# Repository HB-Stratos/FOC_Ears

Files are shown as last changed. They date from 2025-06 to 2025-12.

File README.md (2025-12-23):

Hi there! Since the below was written, a few more things have happened:

You can **send me your Email if you want to get involved with development** and I'll reach out. [Click Here](https://app.formbricks.com/s/cmjj02hcw36xmad01dme5074u).

Work has also started on a PCB based version. PCBs have been ordered, and may or may not have arrived in time for Congress. \
In any case, you can find all KiCad files [on the rev2 branch](https://github.com/HB-Stratos/FOC_Ears/tree/rev-2).

# FOC Ears: Dead Silent Animatronics, a Prototype

This repository documents my work to create truly silent animatronic cat ears.

The classic design using RC airplane servos is quite noisy, and I wanted to fix that to build animatronics that you can comfortably hold a conversation around.

## Table of Contents

- [FOC Ears: Dead Silent Animatronics, a Prototype](#foc-ears-dead-silent-animatronics-a-prototype)
  - [Table of Contents](#table-of-contents)
  - [Status](#status)
    - [Future Plans](#future-plans)
  - [Documentation](#documentation)
    - [System Overview](#system-overview)
      - [Components](#components)
      - [Motor Assembly](#motor-assembly)
    - [Wiring](#wiring)
    - [3D Prints and Mounting](#3d-prints-and-mounting)
    - [Build Environment Setup](#build-environment-setup)
    - [Misc. Lessons Learned](#misc-lessons-learned)
  - [Thanks](#thanks)
  - [Finally](#finally)

## Status

I managed to create a working prototype in time for GPN23. It has a rather bulky perfboard electronics package and several electronic design limitations, such as the lack of a fuse, but it held up well for the entire event. Unfortunately, my phone died between building the prototype and writing this documentation, so I have lost some work-in-progress photographs. Words and renders will have to suffice.

final product

webp animated video

<details>
<summary>More Pictures (expand)</summary>

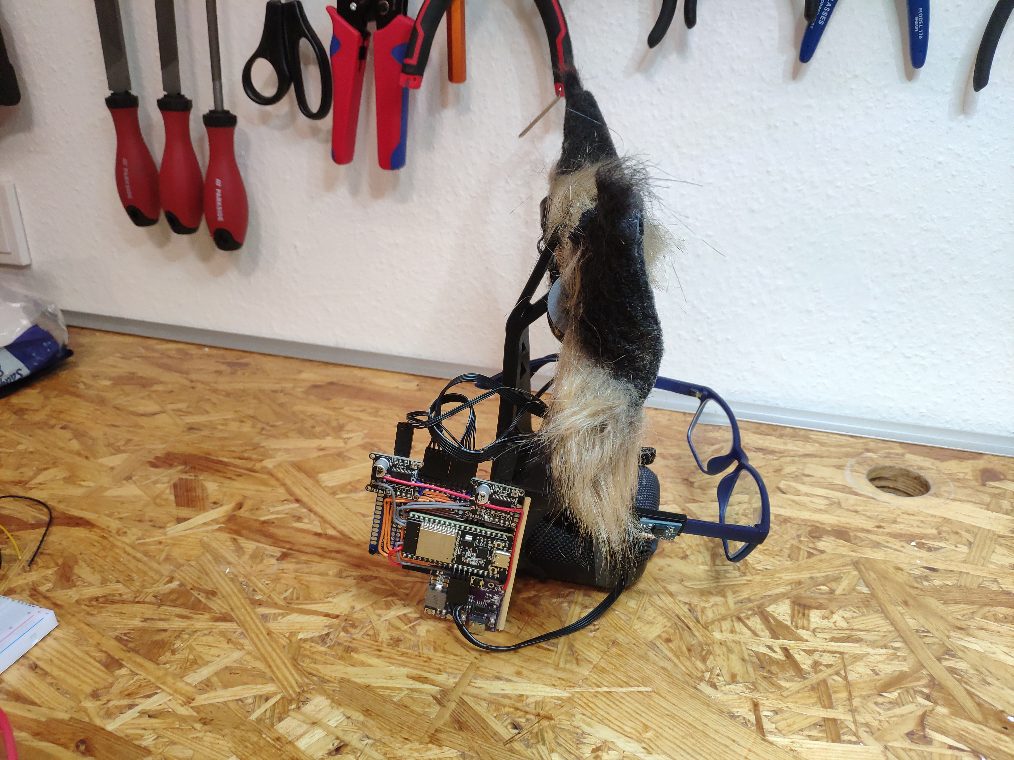
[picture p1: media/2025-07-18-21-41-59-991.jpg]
side view

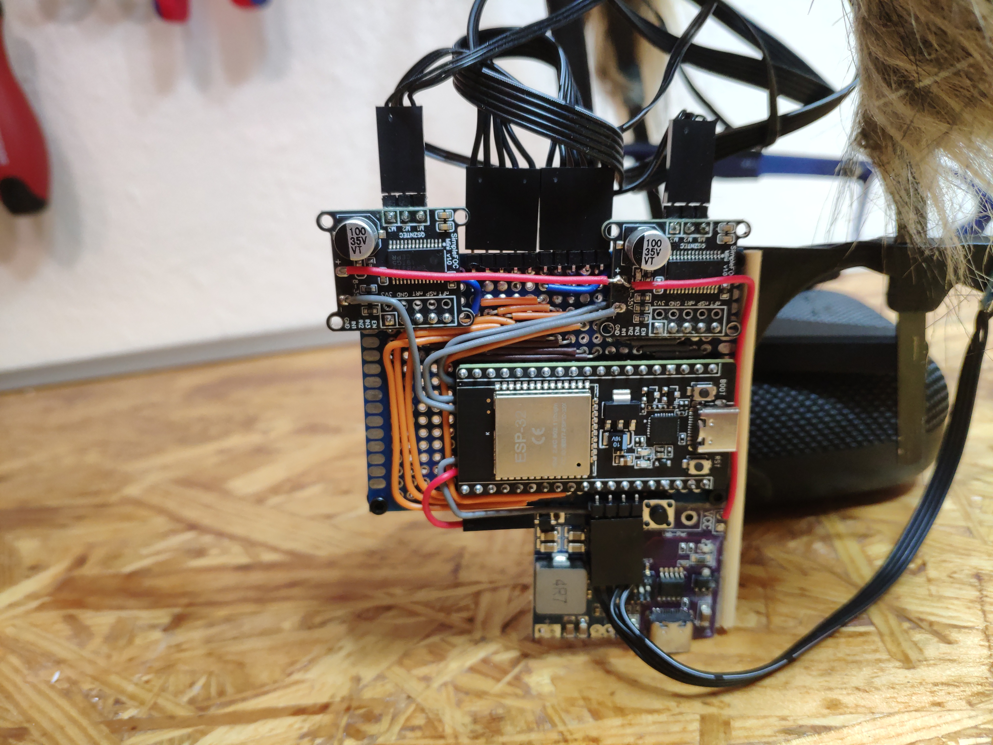
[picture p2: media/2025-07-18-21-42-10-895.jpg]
closeup


</details>

### Future Plans

I plan to develop a more robust version with a printed circuit board between the ears to house the electronics in a much neater way. I would like to eventually create a product out of this development, but even if I do, I plan to keep all design files and details open source.

## Documentation

> [!IMPORTANT] > **This is a prototype**. I am documenting this for sake of posterity. If you wish to replicate this design, you are welcome to do so. However, expect to face issues, poor design decisions and have expect to solve many stupid problems on your own. Because of this, this is not written as a tutorial, but more as an overview of what it takes. That said, I'm happy to help where I can, just leave an issue on the repo here.

With that said, lets get into it

### System Overview

#### Components

The system consists of the following components:

- An [ESP32WROOM](https://aliexpress.com/item/1005008002597306.html) micro controller <br>
  

- Two [SimpleFOC mini](https://docs.simplefoc.com/simplefocmini) driver boards <br>
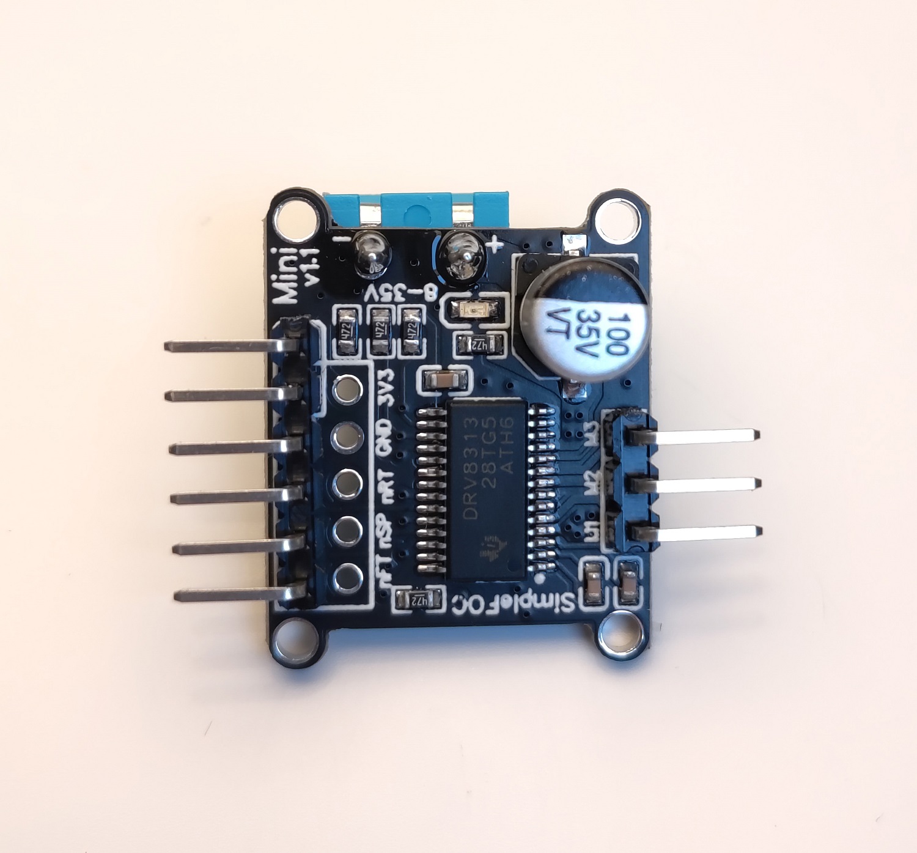
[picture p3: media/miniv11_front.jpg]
  

- Two [Mitoot 2208 100kv](https://aliexpress.com/item/1005006008489660.html) Brushless Gimbal Motors <br>
  

- Two [MT6701qt](https://aliexpress.com/item/1005007349429583.html) Magnetic Encoders <br>
  

- A [BNO055](https://aliexpress.com/item/1005006770124726.html) IMU <br>
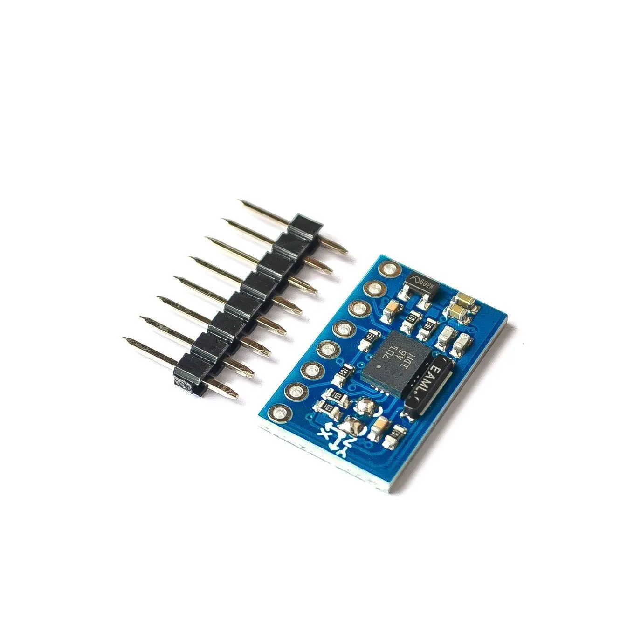
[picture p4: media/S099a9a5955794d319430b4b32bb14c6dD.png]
  

- Ears from Aliexpress. There appears to be a whole range of different style ears on Aliexpress, all following the same basic design. Look for the ears in the ~10€ price class, those will likely be extremely similar to [the ones I used](https://aliexpress.com/item/1005004647818937.html). <br>
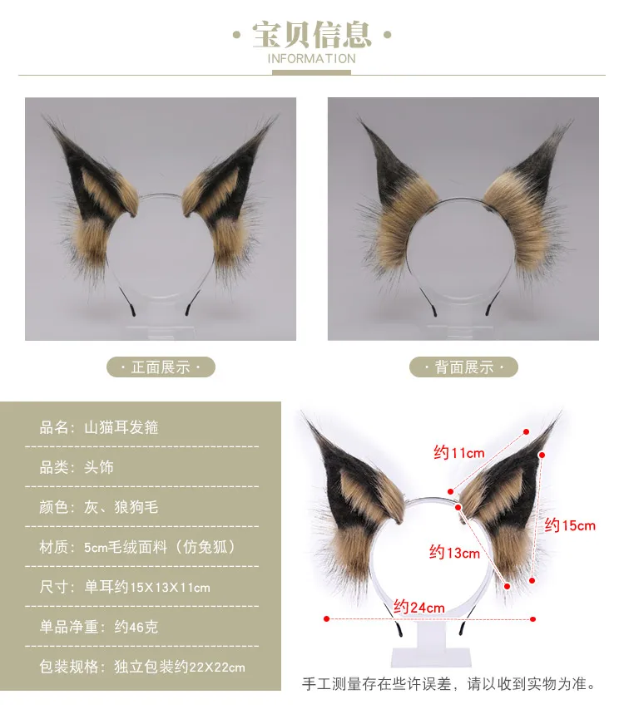
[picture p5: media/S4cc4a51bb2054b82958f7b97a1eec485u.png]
  

- A generic 3.3V Regulator (must be 15V capable)
- A generic configurable USB-C PD trigger board (prototype used 15V)
- A generic USB-C PD capable Power Bank (in my case 100W 20V capable)

Total cost exluding the power bank comes out to ~53€.

Images were taken from their respective linked pages.

> [!NOTE]
> The hardware choices I made worked, but were not ideal:
>
> - The ESP32 can not be flashed without having to hold down the boot button every time
> - The Motors come with the wire through their hub, so one needs to depin the connector, pull the cable through and add the pins again.
> - The Motors are also a bit large, smaller probably works but untested.
> - The Encoder board is undocumented, had to be reverse engineered with the chip data sheet
> - The BNO055 has some hardware issues and is also discontinued, but it was the board I had laying around.

#### Motor Assembly

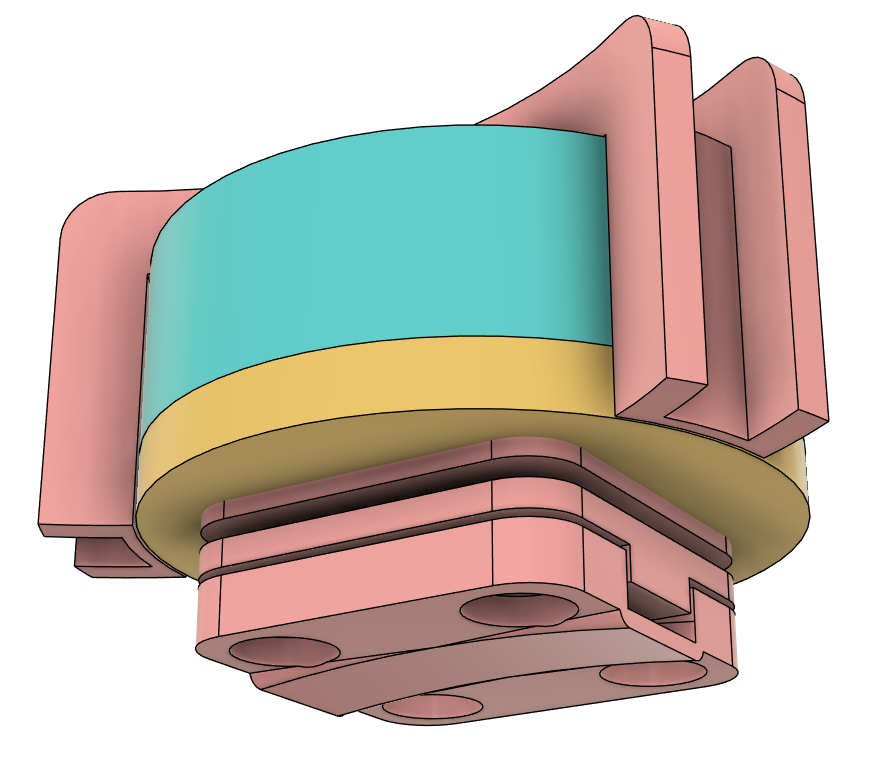
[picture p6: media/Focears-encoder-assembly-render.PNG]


The motor and encoder are mounted together by a stack of parts that clamps the two to each other and the assembly to the head band using all the same screws. The magnet for the encoder is held within the hollow motor shaft by a press fit 3d printed adapter. The ears are mounted on top with two M2x6 screws through the U channel piece.

Ordinarily this wouldn't work as the holes in the motor do not match the holes in the encoder PCB. However there is nothing vital in the ares of the encoder PCB where the holes are needed, so I devised a 3d printed drilling jig to create the required holes. Of course this technique is only applicable to the exact sensor board I used.

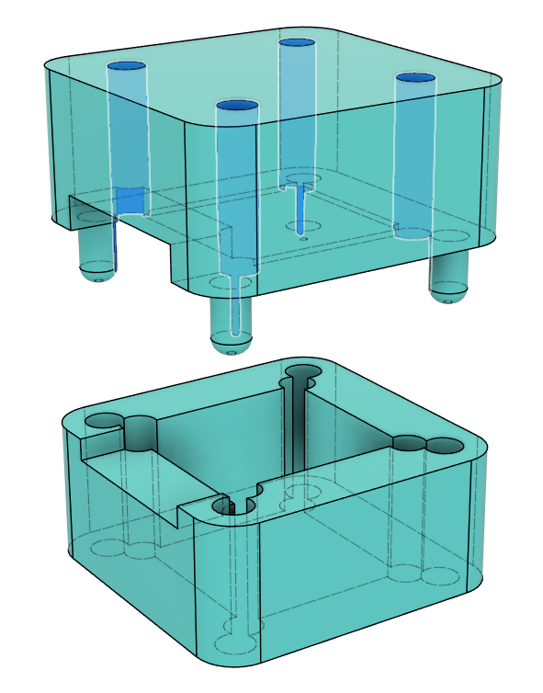
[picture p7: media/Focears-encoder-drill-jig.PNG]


> [!CAUTION]
> Using too long screws to clamp the motor-encoder assembly together will destroy the motor. The holes do not have a backstop, so you will penetrate the coils with the screw. You will not feel rotational resistance as this happens as you are only hitting the stator. I used M2.5x8 screws.

The ears are mounted by making a cutout in them with flush cutters to fit the U channel piece, which is then glued into place with super glue. It is vital that this cut is deeper than the u channel such that the outer edges of the ear sit as flush as possible to the head band. The U channel does not extend all the way down as it would snag on the motor cables if it did.

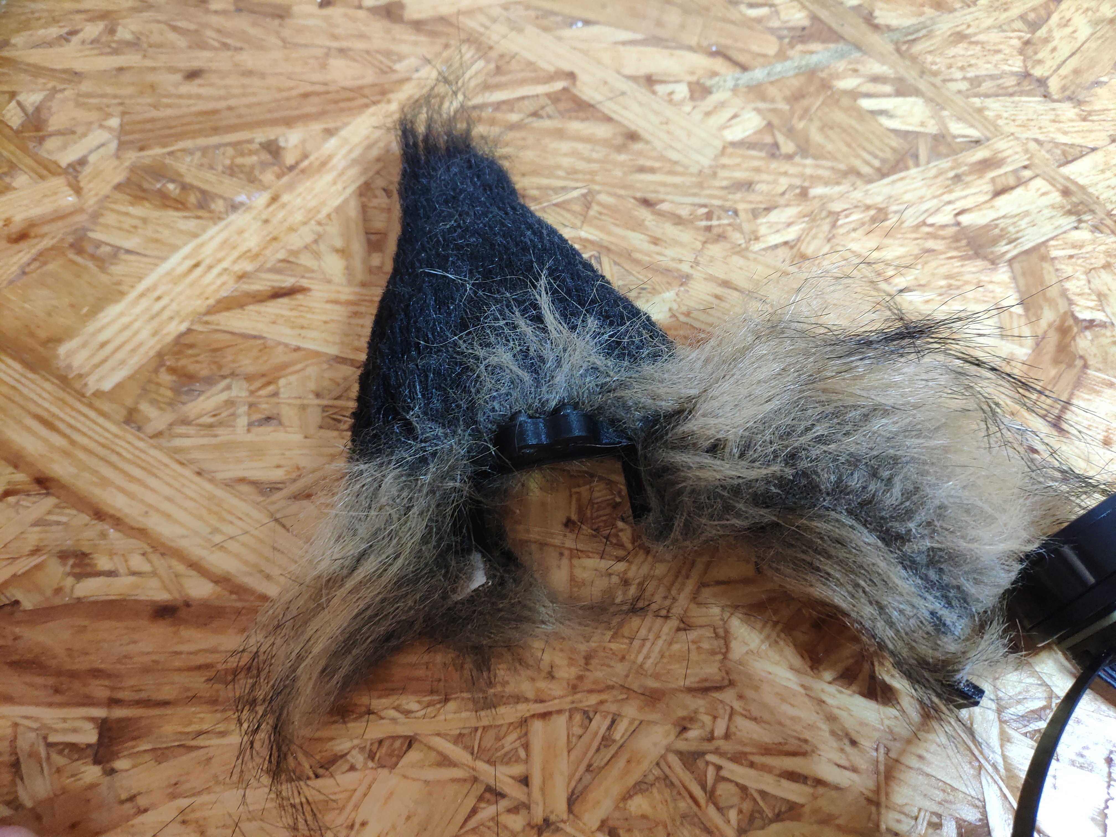
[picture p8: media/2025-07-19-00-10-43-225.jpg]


Additionally, for secondary motion the lower ear lobe of each ear is mounted to a slider on the head band. This causes the ear to fold on rotation, which looks much more natural than the long ear lobe swinging backwards. This however has the issue that the aliexpress ears come with thick wire in them for posing, which would prevent this motion. The solution is as simple as it is ugly: fatigue cracking the wire every 5 or so mm with pliers within the area that should bend. The slider is printed from TPU for silent motion and (surprisingly) low friction.

> [!NOTE]
> I have tried to completely remove the wire from the ears. The wire is hot glued in place within the ears in multiple places, and the fur is bonded together firmly. Even by cutting along the edge of the ear all the way around I was not able to extract the wire in the base of the ear, and said cut looked quite ugly and would have been hard to close up again. Hence I deemed it better to leave the wire in place, but fatigue crack it where necessary. A less hand-fatiguing solution is definitely needed for higher volume production though.

The ear detached from the motor, with lines highlighting roughly where I broke the internal wire. Also visible is the TPU slider, here detached from the rail.



### Wiring

PowerPoint graphic design is my passion. Not pictured are 3.3v running to all sensors, shared ground between all and a 2.2k pullup resistor between SDA and 3.3V on the BNO055. Additionally, note that I used SimpleFOC Mini 1.0 driver boards as they were easily available on Aliexpress. SimpleFOC Mini 1.1 drivers are similar, but their pin order appears to be flipped.

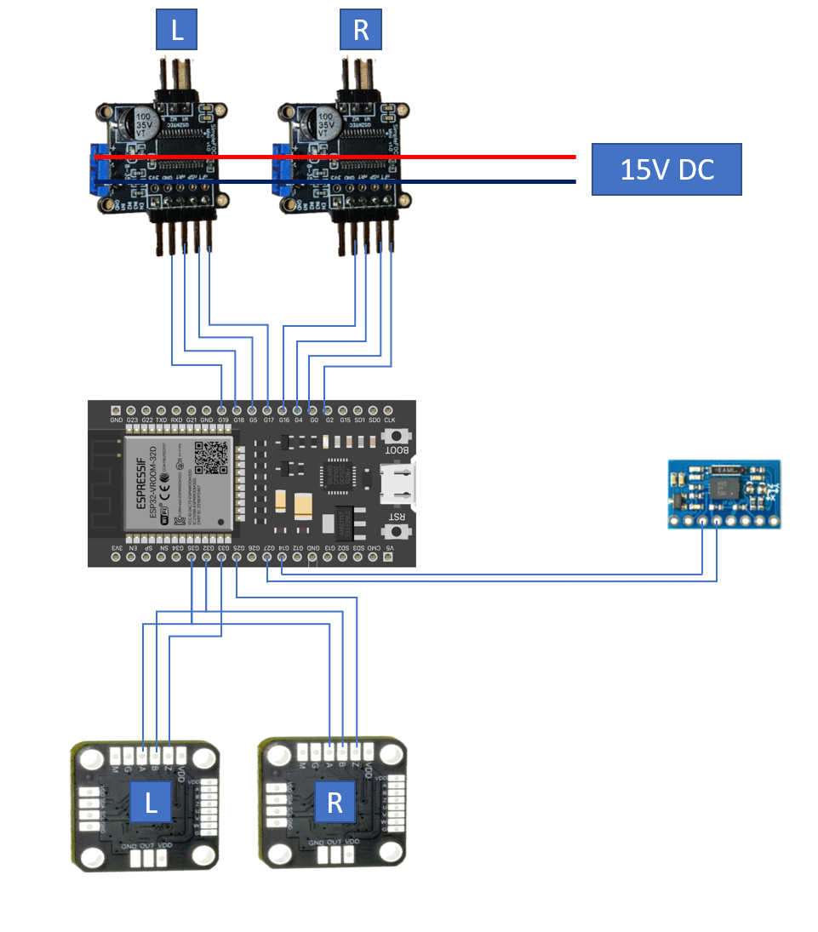
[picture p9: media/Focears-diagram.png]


Here's the reverse-engineered diagram for the encoder. Also, [here's the datasheet](https://uploadcdn.oneyac.com/attachments/files/brand_pdf/magntek/F3/CA/MT6701QT-STD.pdf).

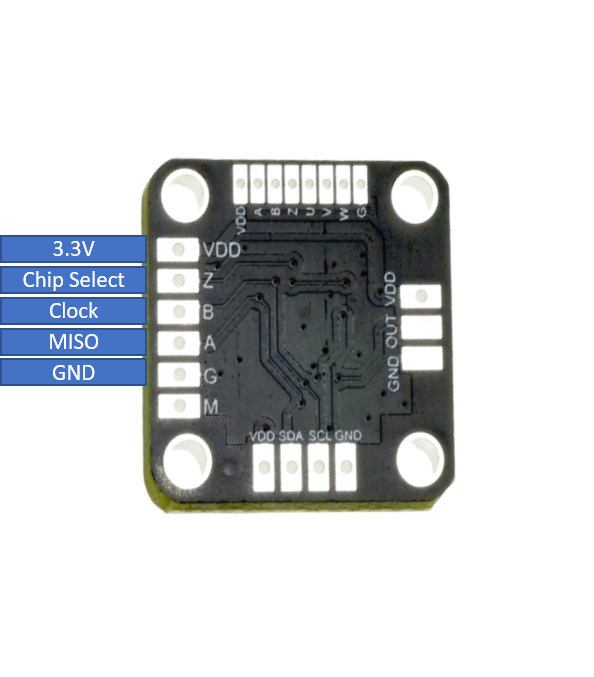
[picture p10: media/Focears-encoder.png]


> [!NOTE]
> This encoder is supposedly capable of I2C and SSI (we use SSI), and CS would toggle between the two modes. However this would cause bad I2C writes on the shared SSI bus with CS off, which I have heard reported, but could never observe myself. I can only assume my specific board has some resistors onboard that disable I2C.

A closeup of the final breadboard. Unsurprisingly, gluing circuit boards together edge to edge did not prove to be particularly sturdy, and the design made the USB-C cable start uncomftably low. But it did work.



### 3D Prints and Mounting

This is the mount for the board, based of my earlier design of ear hook glasses clips to mount non-animatronic ears. This glasses clip is desiged for my glasses (Zenni Optical [Navy Rectangle Glasses #2018916](https://www.zennioptical.com/p/tr-rectangle-eyeglass-frames/20189/2018916) ), so if these do not also happen to be your glasses you will have to devise a custom mounting solution. I am yet to come up with a generic solution that would work with all glasses while still looking good.

Also, this piece is a royal pain to print as one might expect. The first print of it I did completed, but all five attempts to print a spare piece before the event failed.

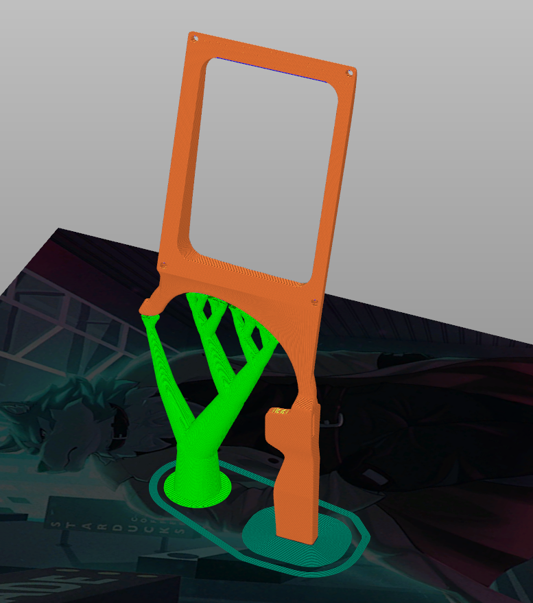
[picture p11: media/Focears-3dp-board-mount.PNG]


The parts constituting one motor-encoder-ear sandwich, laid out in the orientation I printed them in.

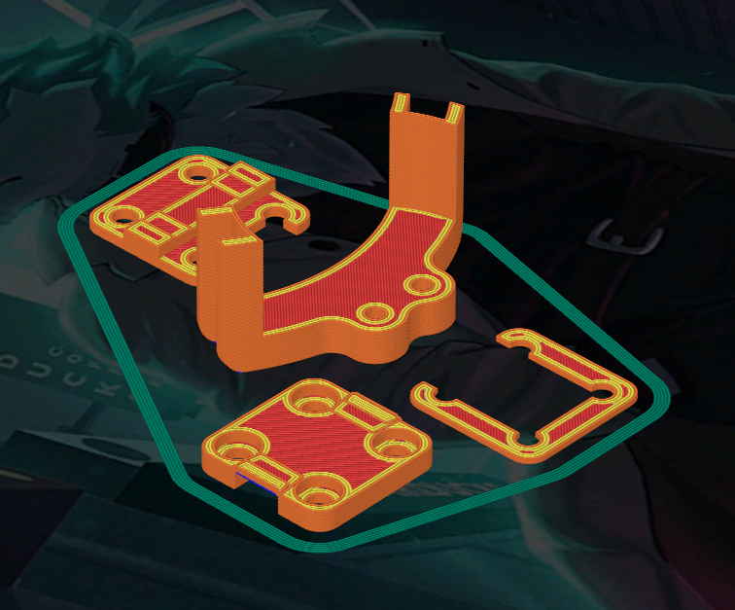
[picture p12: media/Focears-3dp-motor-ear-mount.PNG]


The ear lobe slider which glides on the metal headband. It is printed from TPU for silent motion. Earlier prototypes showed that even the slightest bit of noise so close to the wearer's ear is quite annoying.

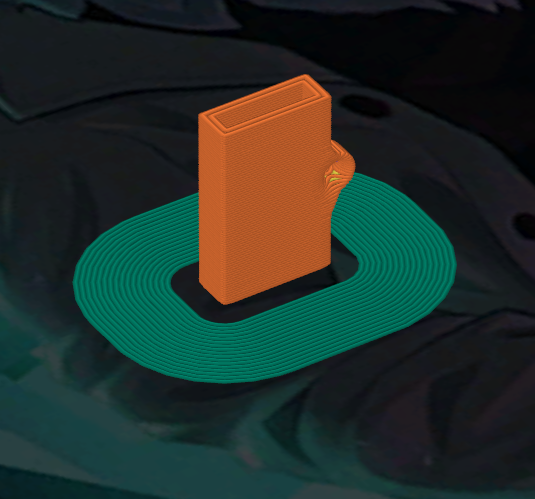
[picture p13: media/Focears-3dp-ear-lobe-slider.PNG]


All 3d printed parts can be found in the `printed_parts` directory as STEP files, as well as the original Fusion360 source files. Do note however that the source files are a royal mess as they were created during prototyping and with exactly zero patience.

### Build Environment Setup

This project uses PlatformIO instead of the Arduino IDE as it has far superior code completion and extension support. Setting up the build environment should just be as easy as setting up PlatformIO using the [official guide](https://docs.platformio.org/en/latest/integration/ide/vscode.html#quick-start) and cloning this repository into the workspace. It will take a few minutes to load, but PlatformIO should automatically download all required frameworks and libraries as specified in the `platformio.ini` file. If this doesn't work for whatever reason, please do open an issue. Also, for some reason this was removed from the official settings, but PlatformIO does offer an "Upload and Monitor (connect to Serial Monitor immediately)" mode. You can find out how to set this up [here](https://community.platformio.org/t/shortcut-to-upload-and-monitor-task-while-also-restarting-it-if-active/18104/5).

### Misc. Lessons Learned

- If the screws clamping the encoder to the motor are not tight enough, the motor likes to shake itself to bits as it twisting against the encoder causes a feedback loop.
- If the screws clamping the encoder to the motor are too tight, they can stretch a poorly printed plastic clamp and make the mounting screws penetrate the motor core.
- Having a cheap oscilloscope ([Zoyi ZT-703S](https://aliexpress.com/item/1005006593085723.html), ~80€) was invaluable during development, you likely want one too.
- At least on my BNO055 board the I2C pullups were too weak for high frequencies, an external pullup was needed.
- Having a Dupont connector crimping tool is quite useful.
- Surprisingly, the mess of wires going from the sensors and motors to the perfboard never got tangled. Still, they're a bad design.
- Having any D term in the PID motion controllers makes the motor quite noisy.
- High loop speed of the main FOC loop is important for precise and silent control.
- Any change in loop speed also constitutes a change in optimal PID values, a fixed loop speed would be a good code design choice I did not make.
- A RP2040 has pretty low loop speed due to lack of a hardware floating point unit, not ideal for this application.
- Many in and output pins are needed to control the motors, 4 per motor driver, one per sensor plus two more sensor shared pins, plus the I2C pins for the IMU. I almost ran out of useable IO pins on the ESP32.
- Reading the IMU every loop slows the motor control loop down too much, reading the IMU every 10 ms was found to be sufficient.
- A PT1 filter element was integrated into the motor driver to limit maximum acceleration, safeguarding from a position step input being too violent.
- The clamping pieces should be printed from ASA or similar, especially during testing or with a sensor error, the motors can get quite hot.
- The metal hoop that comes with the aliexpress cat ears is bent outwards at the bottom. Bending it straight makes sliding mounts with much tighter tolerances on possible.
- Fatigue cracking the ears works, but likes to compress the fur under the pliers. Scratching it with finger nails appears to restore most of the fluff.
- Mounting the ears to my glasses proved essential. The motors are not the lightest, and with my mounting solution clipping onto my glasses and hooking behind my ears, I never feared losing the ears. I am yet to come up with a solution that would work for all glasses frames, let alone a solution for people who do not wear glasses.
- Espressif changed something in more recent versions of the framework, which broke SimpleFOC. It either doesn't compile or kernel panics. I went and found the newest version released before the latest SFOC release, which worked well. You can find the details in the platformio.ini file.
- SimpleFOC requires that PlatformIO `lib_archive = false`. If it isn't your code will compile and run, but behave weirdly in all sorts of strange ways. Be careful.
- The Motors claim they can handle 12V, but I have driven them to 20V with no issues. I just went with 15V as I didn't need the torque and it slowed the motor heating up should an ear become blocked.
- This project started with me trying to use silent stepper drivers and motors for the motion instead of FOC. However, the holding current being constantly drawn by the stepper motors made them get very hot while still lacking torque to not miss steps. Still, using TMC2209 stepper drivers might work for smaller animatronics such as blinking eyes.
- If you can't upload the code with error Access Denied, check if you have a 3D printer slicer such as Cura open. It was automatically trying to connect to all COM ports for me, blocking code uploads.

## Thanks

to everyone who helped me with this project. Especially the amazing people of the Voidstarlab and SimpleFOC discord who took their time to not only help me debug problems with my motor setup, but also with reverse engineering the Encoder PCB, debugging the IMU and many other hardware engineering issues unrelated to SFOC. This was my first true hardware engineering project. I learned a ton, and I couldn't have done it without y'all.

## Finally

Overengineer more silly projects, build cool stuff, and have fun!

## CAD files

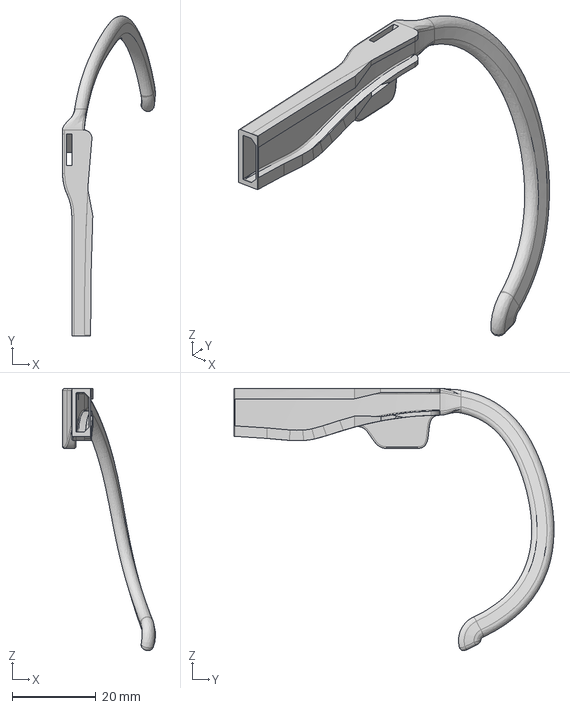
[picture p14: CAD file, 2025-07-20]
printed_parts/FOCEars-glasses-clip-empty.step
22.2 x 76.4 x 62.6 mm

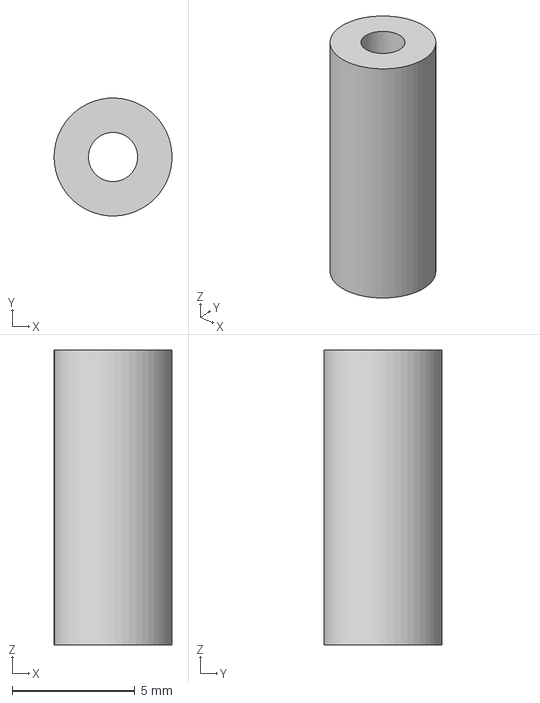
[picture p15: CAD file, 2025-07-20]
printed_parts/FOCEars-motor-encoder-magnet-insert.step
4.80 x 4.80 x 12.0 mm

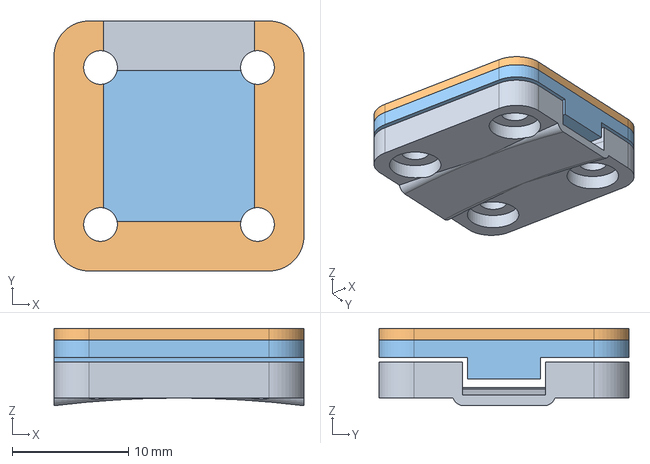
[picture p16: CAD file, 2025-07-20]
printed_parts/FOCEars-motor-mounting-pieces.step
21.5 x 21.5 x 6.66 mm

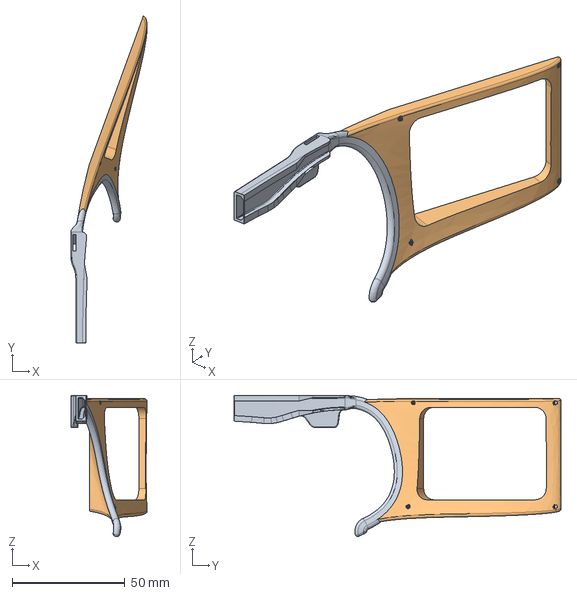
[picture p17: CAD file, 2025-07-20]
printed_parts/FOCEars-glasses-clip-pcb-mount.step
33.9 x 145.0 x 62.6 mm

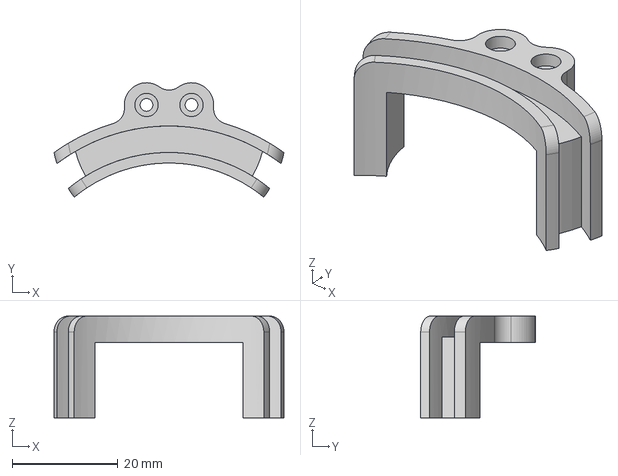
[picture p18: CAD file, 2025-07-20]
printed_parts/FOCEars-u-channel-ear-mount.step
43.5 x 21.6 x 19.2 mm

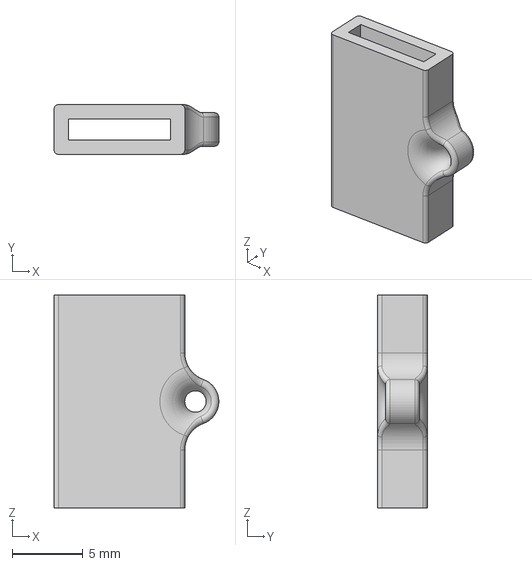
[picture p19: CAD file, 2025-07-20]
printed_parts/FOCEars-tpu-ear-lobe-slider.step
11.6 x 3.50 x 15.0 mm

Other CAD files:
printed_parts/Ear Mount v3.f3z
printed_parts/Ear Silent Slider v3.f3d
printed_parts/Mitoot 2804 Encoder Mount v14 (encoder magnet pin).f3d
printed_parts/Mitoot 2804 Motor Mount v14.f3d
printed_parts/glasses clip v27.f3d

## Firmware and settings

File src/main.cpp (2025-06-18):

#include "Arduino.h"
#include "SPI.h"
#include "SimpleFOCDrivers.h"
#include "encoders/MT6701/MagneticSensorMT6701SSI.h"
#include "EarController.h"
#include <Wire.h>
#include <Adafruit_Sensor.h>
#include <Adafruit_BNO055.h>
#include <IMUHandler.h>
#include <MathHelpers.h>

#define PIN_BUTTON 13

#define I2C_SDA 27
#define I2C_SCL 14

TwoWire I2CBNO = TwoWire(0);
IMUHandler imuHandler(&I2CBNO, 0.5);

EarController earL = EarController(33, 19, 18, 05, 17, 0.1, -1.9);
EarController earR = EarController(25, 16, 04, 00, 02, 0.1, -1.9);

unsigned long leftFlickStartTime = 0;
unsigned long rightFlickStartTime = 0;
const int FLICK_DURATION_MS = 200; // Longer duration for full wave

const unsigned long BUTTON_HOLD_DURATION = 1000; // 1 second in milliseconds
bool buttonPressed = false;
unsigned long buttonPressStartTime = 0;
bool toggleState = false;

float calculateFlick(float progress)
{
    return 0.8f * exp(-4 * progress) * sin(progress * PI * 2);
}

void setup()
{
    Serial.begin(115200);

    I2CBNO.begin(I2C_SDA, I2C_SCL, 100000);
    /* Initialise the sensor */
    if (!imuHandler.init())
    {
        Serial.println("IMU initialization failed!");
        while (1)
            ; // Halt execution if initialization fails
    }

    Serial.println("IMU initialized successfully!");

    /* Initialize Push Button */
    pinMode(PIN_BUTTON, INPUT_PULLUP);

    /* Initialize Ear Controllers */
    earL.setHomePos(0.5);
    earR.setHomePos(-2.9);

    earL.init(2.14, Direction(-1));
    earR.init(1.98, Direction(-1));

    // earL.init();
    // earR.init();
}

unsigned long lastImuUpdate = 0;
unsigned long lastPrintTime = 0;

void loop()
{
    if (digitalRead(PIN_BUTTON) == LOW) // Button is pressed (active LOW)
    {
        if (!buttonPressed)
        {
            // Button just pressed
            buttonPressed = true;
            buttonPressStartTime = millis();
        }
        else
        {
            // Check if button held long enough
            if ((millis() - buttonPressStartTime) >= BUTTON_HOLD_DURATION)
            {
                toggleState = !toggleState; // Flip the toggle
                // Reset timer to prevent multiple toggles
                buttonPressStartTime = millis();
            }
        }
    }
    else
    {
        buttonPressed = false;
    }

    float targetAngle = 0.1 * PI * _sin(float(millis()) / 500 * PI);
    float targetR = 0;
    float targetL = 0;

    // Use toggleState instead of direct button reading
    if (toggleState)
    {
        targetL =
            +utils::remap_clamped(imuHandler.getAbsoluteRotation().z(), -0.8, -PI / 2, 1, 0.1) + utils::remap_clamped(imuHandler.getAbsoluteRotation().y(), PI / 2, -0.1, 0.9, 0);

        targetR =
            +utils::remap_clamped(imuHandler.getAbsoluteRotation().z(), -PI + 0.8, -PI / 2, 1, 0.1) + utils::remap_clamped(imuHandler.getAbsoluteRotation().y(), PI / 2, -0.1, 0.9, 0);

        unsigned long currentTime = millis();

        // Initiate new flicks
        if (random(100000) < 5 && currentTime - leftFlickStartTime > FLICK_DURATION_MS)
        {
            leftFlickStartTime = currentTime;
        }
        if (random(100000) < 5 && currentTime - rightFlickStartTime > FLICK_DURATION_MS)
        {
            rightFlickStartTime = currentTime;
        }

        // Apply flick animations
        if (currentTime - leftFlickStartTime < FLICK_DURATION_MS)
        {
            float progress = float(currentTime - leftFlickStartTime) / FLICK_DURATION_MS;
            targetL += calculateFlick(progress);
        }

        if (currentTime - rightFlickStartTime < FLICK_DURATION_MS)
        {
            float progress = float(currentTime - rightFlickStartTime) / FLICK_DURATION_MS;
            targetR += calculateFlick(progress);
        }
    }

    // earL.moveTo(targetAngle);
    // earR.moveTo(targetAngle);

    earL.move01(targetL);
    earR.move01(1 - targetR);

    earL.update();
    earR.update();

    if (millis() - lastImuUpdate >= 10)
    {
        imuHandler.update();
        lastImuUpdate = millis();
    }

    if (millis() - lastPrintTime >= 100)
    {
        // Serial.print("L: ");
        // Serial.print(earL.getAngle());
        // Serial.print(" R: ");
        // Serial.print(earR.getAngle());
        Serial.print(" Target: ");
        Serial.print(targetAngle);
        // Serial.println("");

        lastPrintTime = millis();

        imu::Vector<3> var = imuHandler.getAbsoluteRotation();
        Serial.print("X: ");
        Serial.print(var.x());
        Serial.print(" Y: ");
        Serial.print(var.y());
        Serial.print(" Z: ");
        Serial.print(var.z());
        Serial.println("");
    }

    /* Absolute Rotations:
    X: Pitch, zero @ 180, pitch up is decrease
    Y: Roll, zero @ -90, roll right is increase
    Z: Yaw, zero irrelevant
    */

    /*Angular Velocities:
    X: Yaw
    Y: Roll, roll right is increase
    Z: Pitch, pitch up is increase
    */

    /*Linear Accelerations:
    X: Up, upwards is positive
    Y: Forwards, forward is negative
    Z: Rightwards, right is negative
    */

    // _delay(100);
}

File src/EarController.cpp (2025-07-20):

#include "EarController.h"

// Constructor
EarController::EarController(int senCs, int pwm1, int pwm2, int pwm3, int drvEnable, float minAngle, float maxAngle)
    : myMT6701SPISettings(4000000, MT6701_BITORDER, SPI_MODE2),
      sensor(senCs, myMT6701SPISettings),
      driver(pwm1, pwm2, pwm3, drvEnable),
      motor(7, 11.2, 80, 0.003),
      lpf(0.02),
      minAngle(minAngle), // Initialize minAngle
      maxAngle(maxAngle)  // Initialize maxAngle
{
    DEBUG_PRINT("EarController initialized.");
}

// Destructor
EarController::~EarController()
{
    DEBUG_PRINT("EarController destroyed.");
}

// Public function: Initialize the controller
void EarController::init(float zero_electric_offset, Direction sensor_direction)
{
    DEBUG_PRINT("Initializing EarController...");

    motor.zero_electric_angle = zero_electric_offset;
    motor.sensor_direction = sensor_direction;

    // MOSI is not used at all, but has to be specified
    SPI.begin(32, 35, 33); // TODO clean up SPI bus
    configureDriver();
    configurePID();

    motor.linkSensor(&sensor);
    motor.linkDriver(&driver);

    sensor.init();
    driver.init();
    motor.init();

    if (motor.initFOC())
        Serial.println("FOC init success!");
    else
    {
        Serial.println("FOC init failed!");
        return;
    }

    DEBUG_PRINT("Sensor electric offset: ");
    DEBUG_PRINT(motor.zero_electric_angle);
    DEBUG_PRINT("Sensor Direction: ");
    DEBUG_PRINT(motor.sensor_direction);

    DEBUG_PRINT("Initialization complete.");
}

// Public function: Move to a specific angle
void EarController::moveTo(float targetAngle)
{
    motor.move(lpf(targetAngle));
}

// Public function: Move between minAngle and maxAngle based on input [0, 1]
void EarController::move01(float input)
{
    float targetAngle = utils::remap_clamped(input, 0.0f, 1.0f, minAngle, maxAngle);
    motor.move(targetAngle);
}

// Public function: Update the motor state
void EarController::update()
{
    motor.loopFOC();
}

void EarController::setHomePos(float homeAngle)
{
    motor.sensor_offset = homeAngle;
}

float EarController::getAngle()
{
    sensor.update();
    return sensor.getAngle();
}

// Setters for minAngle and maxAngle
void EarController::setMinAngle(float angle)
{
    minAngle = angle;
}

void EarController::setMaxAngle(float angle)
{
    maxAngle = angle;
}

// Private function: Configure the driver
void EarController::configureDriver()
{
    DEBUG_PRINT("Configuring driver...");

    // pwm frequency to be used [Hz]
    driver.pwm_frequency = 24000;
    // power supply voltage [V]
    driver.voltage_power_supply = 15;
    // Max DC voltage allowed - default voltage_power_supply
    driver.voltage_limit = 15;
}

// Private function: Configure PID settings
void EarController::configurePID()
{
    DEBUG_PRINT("Configuring PID...");

    // set control loop type to be used
    motor.controller = MotionControlType::angle;

    // velocity PID controller parameters
    // default P=0.5 I = 10 D =0
    motor.PID_velocity.P = 0.02;
    motor.PID_velocity.I = 2;
    motor.PID_velocity.D = 0.00;
    // jerk control using voltage voltage ramp
    // default value is 300 volts per sec  ~ 0.3V per millisecond
    motor.PID_velocity.output_ramp = 0;

    // velocity low pass filtering
    // default 5ms - try different values to see what is the best. m,
    // the lower the less filtered
    motor.LPF_velocity.Tf = 1 / (6.28 * 200);

    // setting the limits
    // either voltage
    // motor.voltage_limit = 10; // Volts - default driver.voltage_limit
    // // of current
    // motor.current_limit = 2; // Amps - default 0.2Amps

    // angle PID controller
    // default P=20
    motor.P_angle.P = 20;
    motor.P_angle.I = 0; // usually only P controller is enough
    motor.P_angle.D = 0; // usually only P controller is enough
    // acceleration control using output ramp
    // this variable is in rad/s^2 and sets the limit of acceleration
    motor.P_angle.output_ramp = 0; // default 1e6 rad/s^2

    // angle low pass filtering
    // default 0 - disabled
    // use only for very noisy position sensors - try to avoid and keep the values very small
    motor.LPF_angle.Tf = 0; // default 0

    // setting the limits
    //  maximal velocity of the position control
    motor.velocity_limit = 10000; // rad/s - default 20

    // motor.PID_velocity.limit = 1;
    // motor.P_angle.limit = 200;
}

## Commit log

2025-06-18 update filter plotter still broken
2025-06-18 made button toggle
2025-07-20 (finally) wrote some documentation
    [Ear Mount v3.f3z, Ear Silent Slider v3.f3d, FOCEars-glasses-clip-empty.step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]
